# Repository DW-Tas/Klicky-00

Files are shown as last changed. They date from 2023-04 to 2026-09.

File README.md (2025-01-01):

[][cc-by-nc-sa]

# Klicky-00: Zero X,Y offset probe (RC3)

Building on the amazing work of JosAr ([Klicky Probe](https://github.com/jlas1/Klicky-Probe)), whoppingpochard ([PCB Klicky](https://github.com/tanaes/whopping_Voron_mods/tree/main/pcb_klicky)), and Majarspeed ([Unklicky](https://github.com/majarspeed/Unklicky)) this mod moves the probe directly under the nozzle (X,Y 0,0) and also has the nozzle touching the probe so that you can reliably use it as your z endstop with consistent z-offset. All the usual caveats about clean nozzles during probing apply here too.

The goal of this probe is to give accurate, nozzle probe-like, repeatable Z-offset on a budget even when changing nozzles.

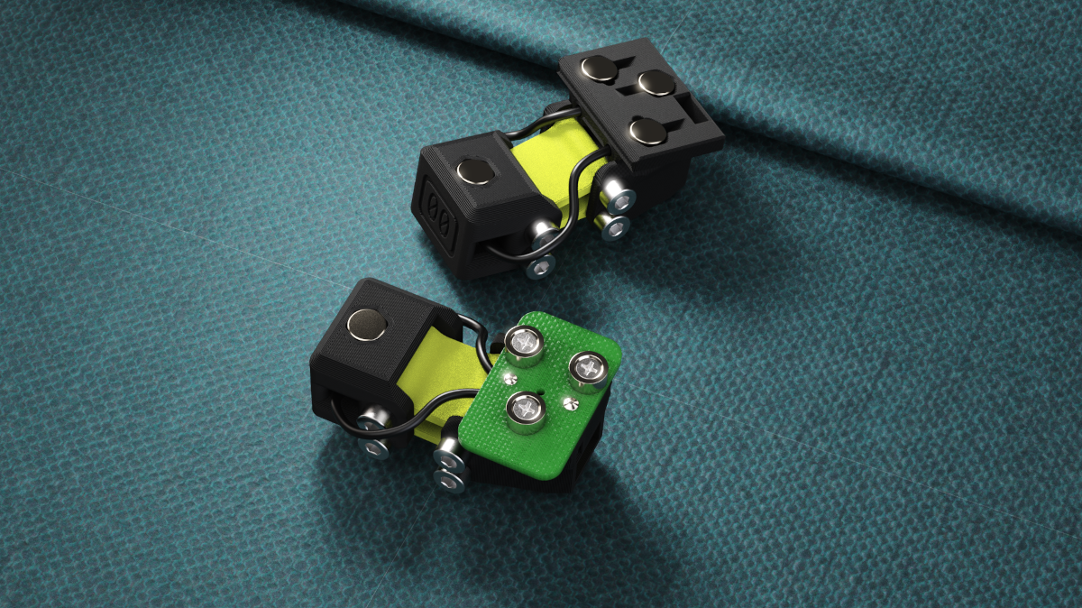
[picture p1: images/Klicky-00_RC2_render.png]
render

<br/> <br/>

<br/> <br/> <br/> <br/>
> [!NOTE]  
> You can help support the development of Klicky-00.<br/>
> Click on the Ko-Fi image below.<br/>

ko-fi (https://ko-fi.com/O5O5OCC0K)

<br/> <br/> <br/>

#### Constraints:
* Low cost
* Easy access to required parts
* Simple add-on to existing ecosystems

### Currently in "release candidate (RC)" status
Versions have been community tested on Xol Toolhead, Archetype and Stealthburner. Many gremlins have been worked out already, but things are still being found as more and more people join the fun of Klicky-00.

### Discussion and development on the Armchair discord

Join us on Discord (https://discord.gg/armchairengineeringsux)<br/>
Find the [Klicky-00 thread](https://discord.com/channels/1029426383614648421/1101496347540082799) under "user-projects"

#### RC3 - 01/01/2025
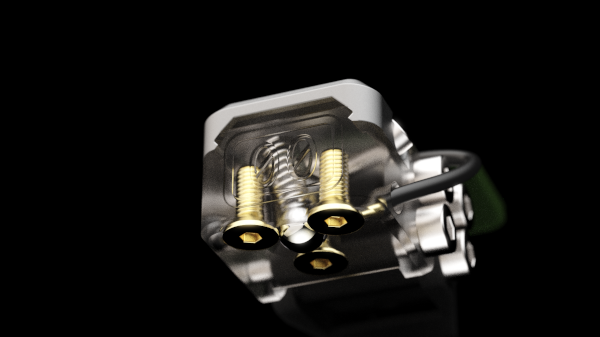
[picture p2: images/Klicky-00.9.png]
Buckshot transparent

* Swingarm fixes for better location of probe under nozzle
* Changed Buckshot switches to use FHCS screws
* CAD fixes

#### RC2 - 05/05/2024
* Changed swingarm hinge screws to M3 (no more M2.5 screws needed)
* Increased strength around hinge points
* Moved D2F switch location to properly match 0,0 concept
* `New Switch Type` `Beta` Buckshot switch by ZaMarin <br/><br/>
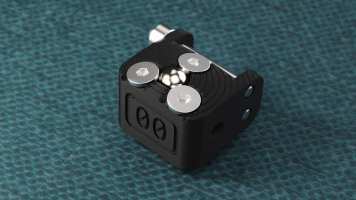
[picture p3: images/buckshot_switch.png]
buckshot switch
  

### Use 6mm x 3mm magnets
I have designed this around 6x3mm magnets and it will probably fail with the 6x2.7mm magnets that are also common. A mix of N52 and N35 magnets are most likely needed to help "tune" attraction and spring forces.

### Build Guide
Go to the [instructions](instructions.md)

### But why another probe?
Like many others, I installed Voron TAP and loved the consistency, repeatability and user experience, but I didn't like the extra complexity, weight and instability added to the toolhead.
I had previously used KlickyNG with auto-z calibration scripts and while that was good, I ALWAYS had to watch the first layer and make micro-adjustments to Z offset.

This probe takes the reliable docking hardware and software of the PCB Klicky and the high accuracy of the Unklicky BFP and puts them in contact with the probe for repatable z-offset and zero XY offset.

Initial testing in a Voron 2.4R2(300mm) with Xol-Toolhead looks promising.
probe_accuracy standard deviation results vary from 0.0005 to 0.0025 on my printer and that is similar to what I got with TAP.

Drift was also very low with bed temp at 118°C, nozzle 200°C and chamber ~57°C

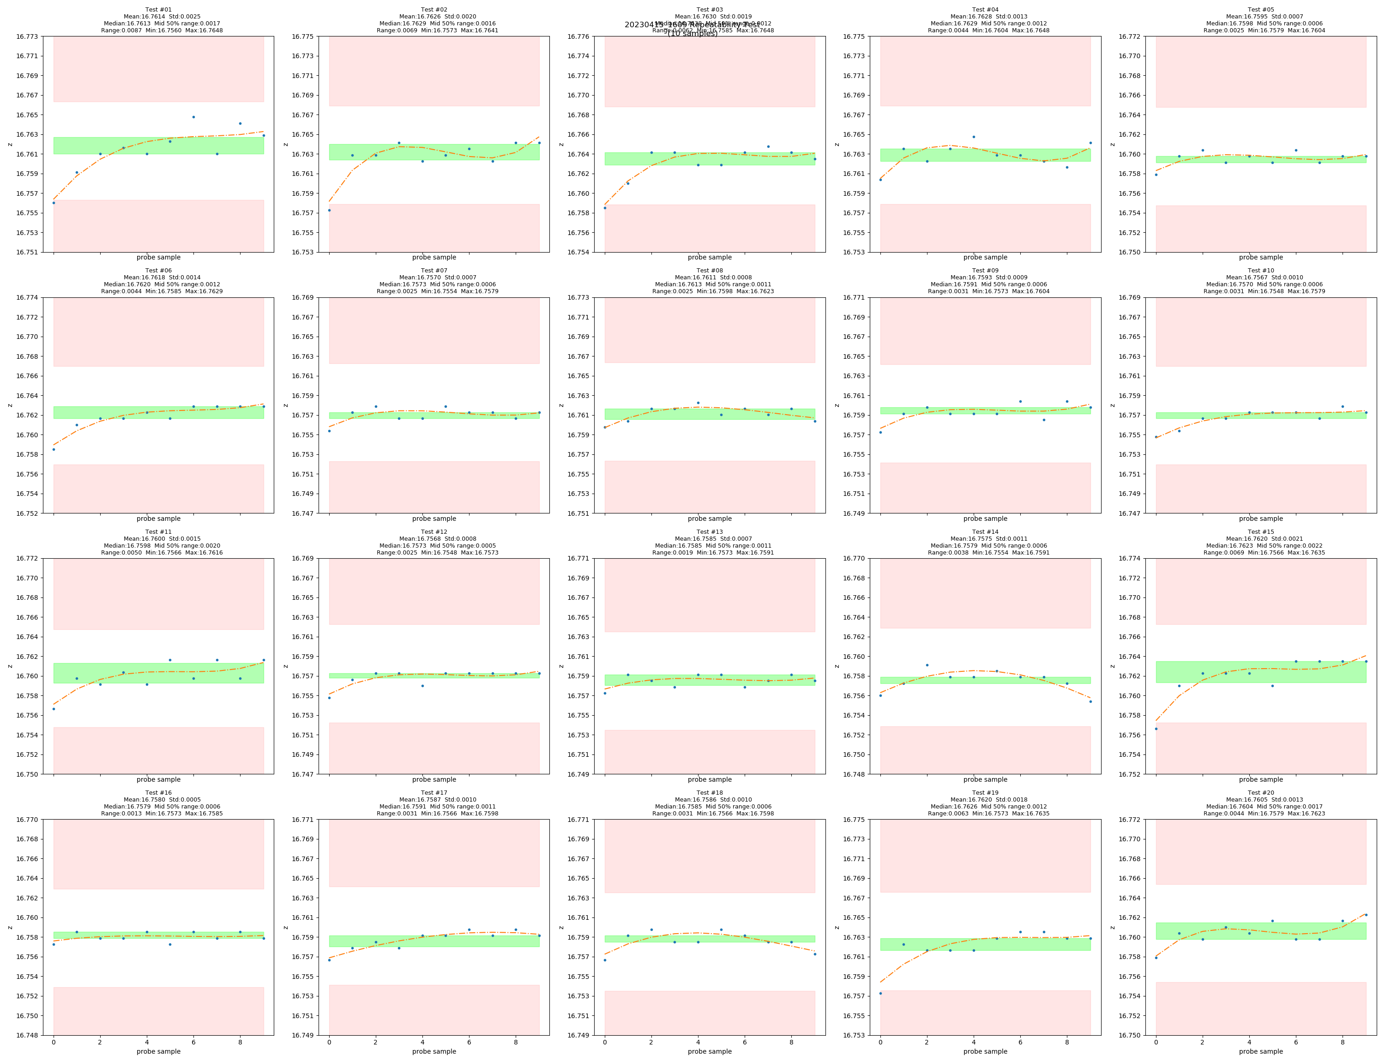
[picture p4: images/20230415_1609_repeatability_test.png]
repeatability_test

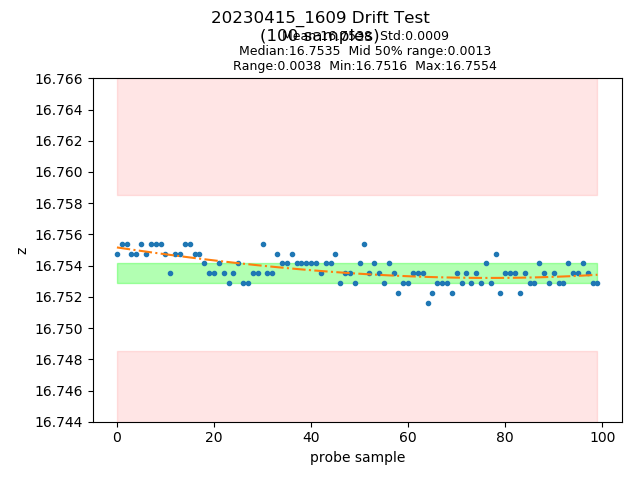
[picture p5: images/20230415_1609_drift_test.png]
drift_test


### Credits:
* ZaMarin - For the Buckshot switch mechanism, and inspiring the linkage design that unlocked Klicky-00s potential and the continued help behind the scenes.

### References:
* [Klicky Klipper macros](https://github.com/jlas1/Klicky-Probe/tree/main/Klipper_macros)
* [Unklicky build guide](https://github.com/majarspeed/Unklicky/blob/main/Build%20Guide.md)
* [Voron Docs Klicky as Z-endstop](https://docs.vorondesign.com/community/howto/Takuya/Klicky_Probe_AutoZ_Alternative.html)

<br/><br/><br/><br/>
This work is licensed under a
[Creative Commons Attribution-NonCommercial-ShareAlike 4.0 International License][cc-by-nc-sa].

[][cc-by-nc-sa]

[cc-by-nc-sa]: http://creativecommons.org/licenses/by-nc-sa/4.0/
[cc-by-nc-sa-image]: https://licensebuttons.net/l/by-nc-sa/4.0/88x31.png
[cc-by-nc-sa-shield]: https://img.shields.io/badge/License-CC%20BY--NC--SA%204.0-lightgrey.svg

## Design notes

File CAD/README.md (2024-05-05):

### Finally some release candidate CAD 😄

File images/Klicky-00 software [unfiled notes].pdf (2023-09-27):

# Klicky-00 software

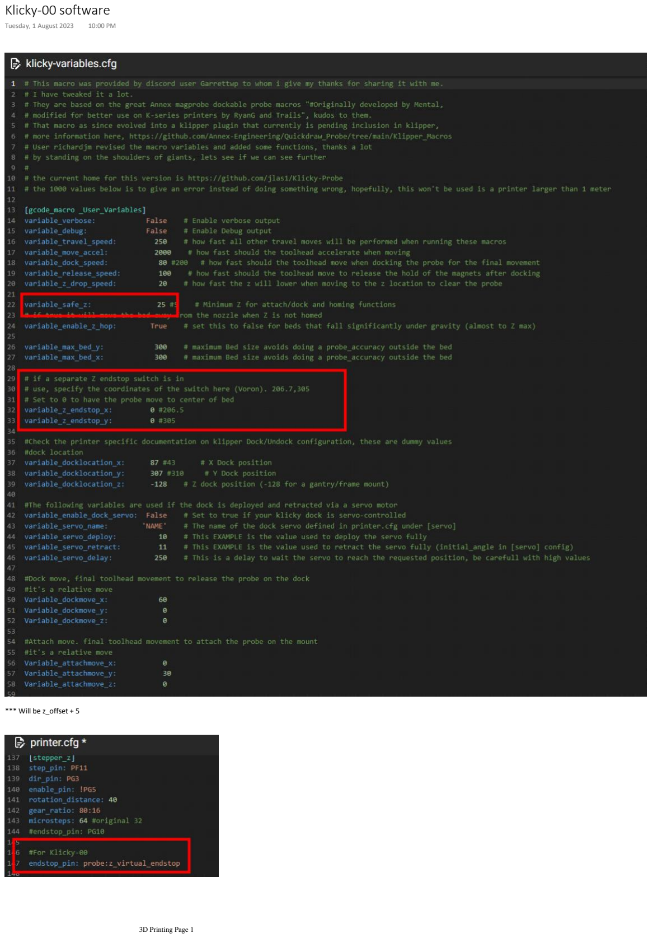
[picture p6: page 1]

*** Will be z_offset + 5

Tuesday, 1 August 2023 10:00 PM

3D Printing Page 1

****for setup only set "position_min: -25" (in the stepper_z section)
** DANGER: set this back to -5 after setup. You need to be able to go much further below zero when first doing "probe_calibrate" with Klicky-00

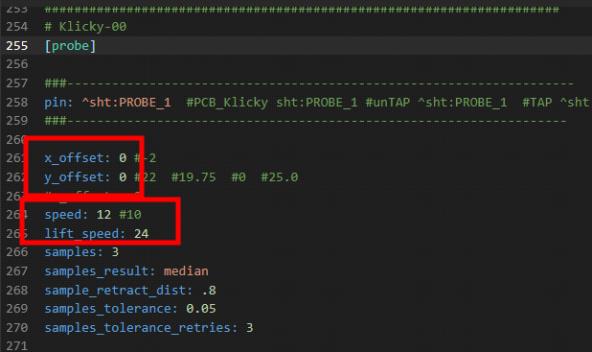
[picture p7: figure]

* [z_offset] +5 is pretty safe

*[z_offset] + retract distance gives fasted mesh

****** After running probe_calibrate locate z_offset that was saved at the end of printer.cfg

3D Printing Page 2

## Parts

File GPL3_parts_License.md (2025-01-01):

The custom STLs that come from GPL3 projects remain under the GPLv3 license.
<br/><br/>
These parts are the rear parts of the probe that include the Klicky and Klicky PCB docking and attachment geometry:
* Klicky-00_Klicky_Rear
* Klicky-00_PCB_Klicky_Rear

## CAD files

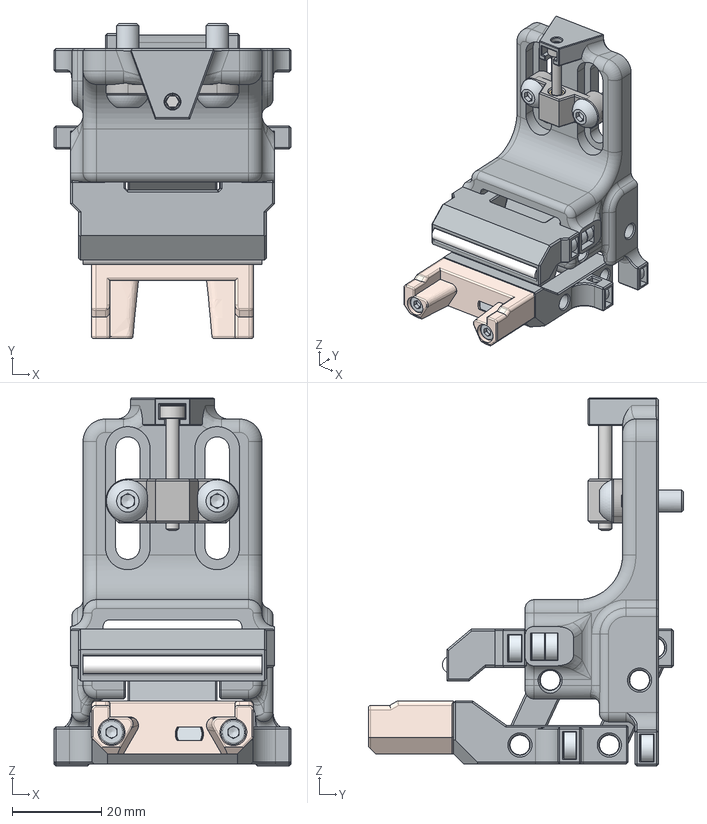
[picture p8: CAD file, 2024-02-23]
CAD/Klicky-00_Bump-Dock_assembly.step
53.0 x 70.4 x 82.3 mm
Klicky-00_front_magnet x 5
Lowerbody
PTFE Tube
arm1
Socket button head screw M5x0.8 x 16 x 2
M3 Threaded Insert (1) v1 x 3
height-adjuster
M3x25 SHCS
Mainbody
bumper
Klicky-00 PCB dock
Klicky-00_rear_magnet
Hex socket head cap screw M3x0.50 x 20 x 2
arm2

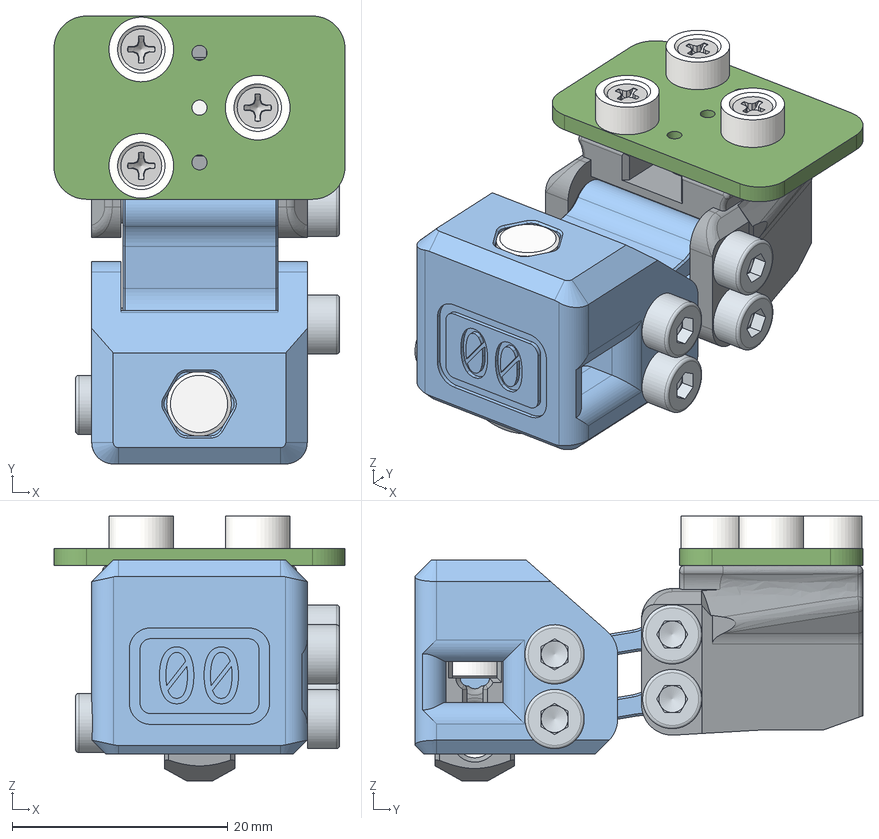
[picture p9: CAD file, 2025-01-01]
CAD/Klicky-00 - RC3 Assembled probes/Klicky-00 Archetype Unklicky PCB.step
27.0 x 41.6 x 24.6 mm
Klicky-00_Archetype_Swingarm_Lower
Klicky-00_Archetype_Swingarm_Upper
Hex socket head cap screw M3x0.50 x 20 x 4
Klicky-00_Archetype_Unklicky_Front
Klicky-00_Unklicky_Stylus
Hex socket head cap screw M3x0.50 x 12
6x3 Magnet x 5
Klicky-00_PCB_Klicky_Rear
pcb
94180A307_Tapered Heat-Set Inserts for Plastic x 3
Magnets x 3
91420A003_Steel Phillips Flat Head Screws x 3

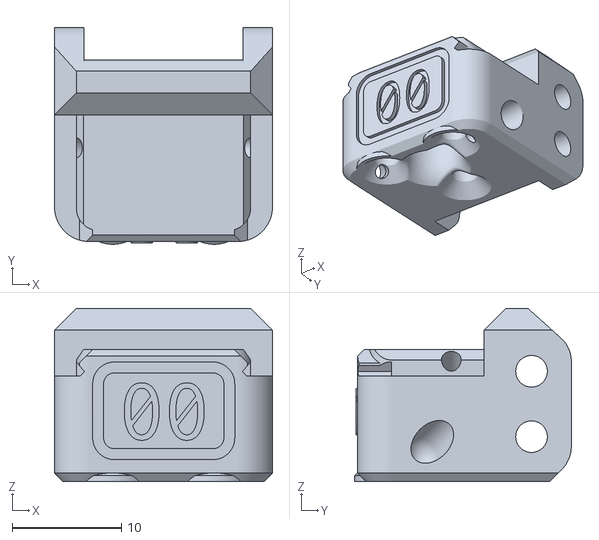
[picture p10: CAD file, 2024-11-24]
STL/SLM Nozzle Plate/Klicky-00_A4T-Xol_Buckshot_Front-Strike_SLM.stl
20.0 x 19.9 x 15.9

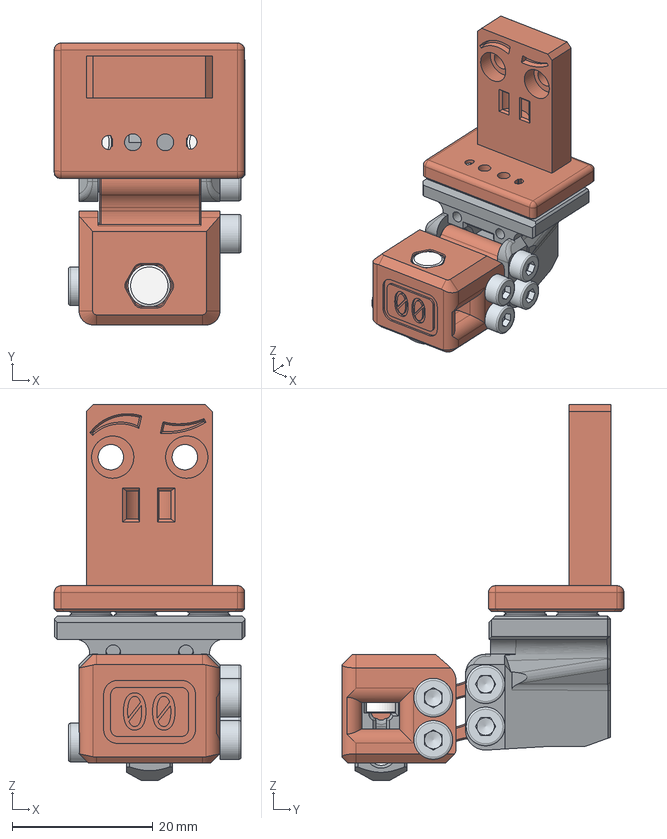
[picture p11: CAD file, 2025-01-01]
CAD/Klicky-00 - RC3 Assembled probes/Klicky-00 SB Unklicky Klicky.step
27.1 x 40.0 x 53.3 mm
Klicky-00_SB_Swingarm_Upper
6x3 Magnet x 11
Klicky-00_SB_Swingarm_Lower
Hex socket head cap screw M3x0.50 x 20 x 4
Klicky-00_Klicky_Rear
Klicky-00_Klicky_Mount_SB
Klicky-00_Unklicky_Stylus
Klicky-00_SB_Unklicky_Front
Hex socket head cap screw M3x0.50 x 12

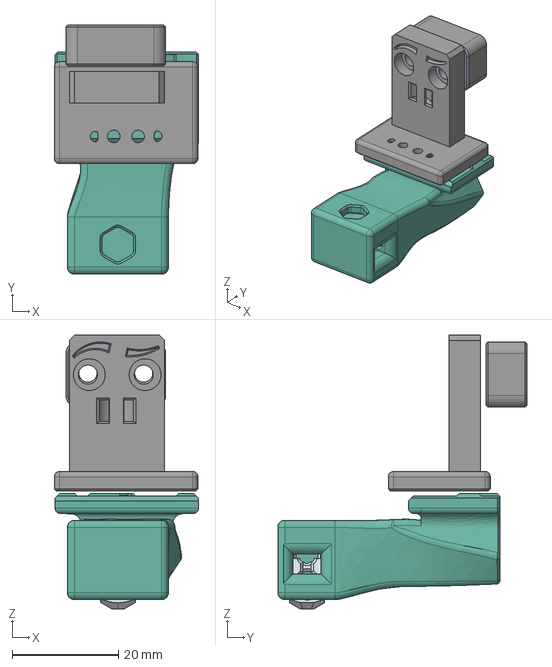
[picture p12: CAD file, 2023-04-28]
CAD/Klicky-00_SB.step
27.2 x 47.0 x 51.6 mm

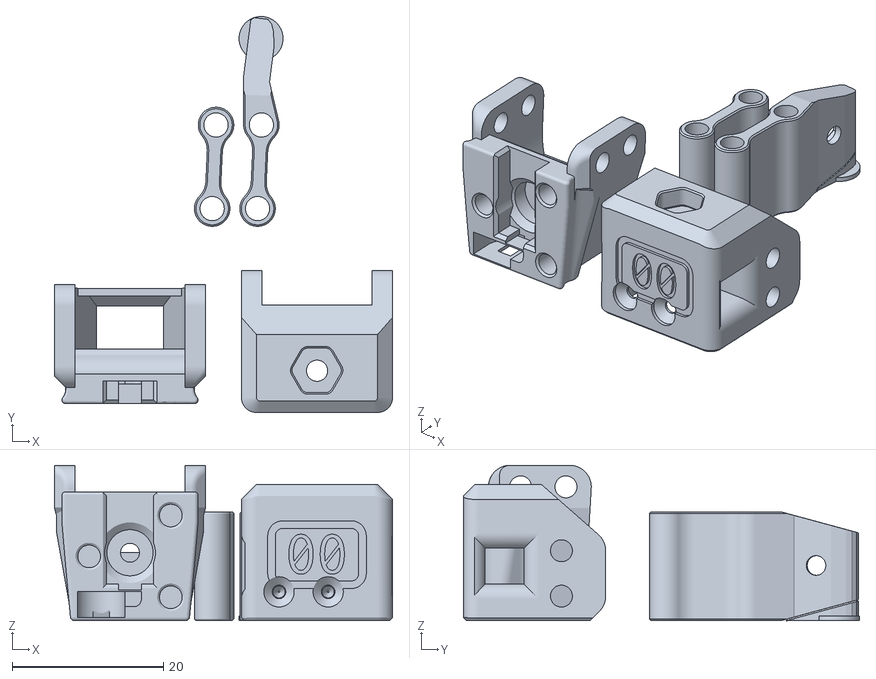
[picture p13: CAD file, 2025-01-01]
STL/Archetype - D2F - PCB.stl
44.7 x 52.4 x 20.5

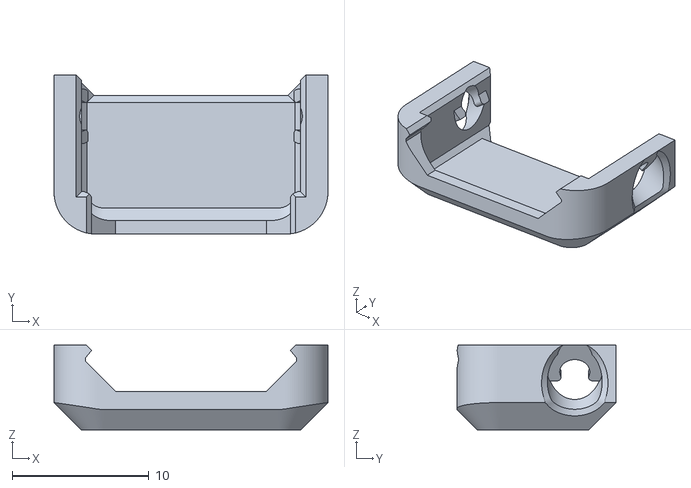
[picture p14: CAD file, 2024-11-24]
STL/SLM Nozzle Plate/Klicky-00_SLM_Nozzle_Plate.stl
20.0 x 11.6 x 6.20

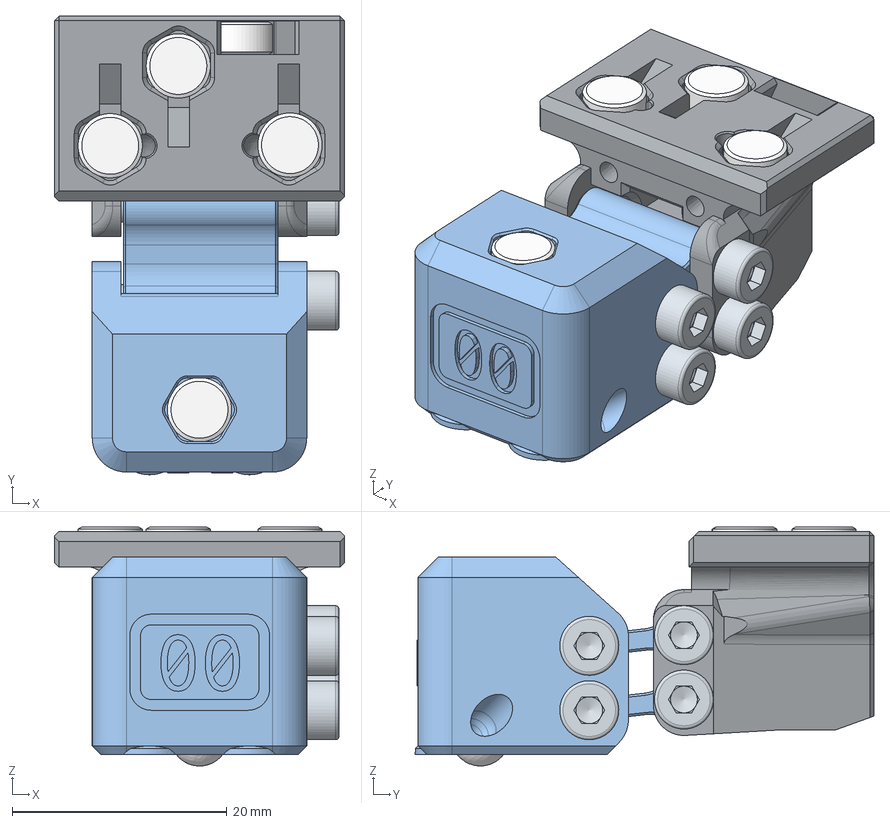
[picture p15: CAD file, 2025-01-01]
CAD/Klicky-00 - RC3 Assembled probes/Klicky-00 Archetype Buckshot Klicky.step
27.0 x 42.7 x 22.3 mm
6x3 Magnet x 7
Klicky-00_Archetype_Swingarm_Lower_Buckshot
Klicky-00_Archetype_Swingarm_Upper_Buckshot
Hex socket head cap screw M3x0.50 x 20 x 4
Klicky-00_Archetype_Buckshot_Front
BB
M3x8 FHCS x 3
Spring
Klicky-00_Klicky_Rear

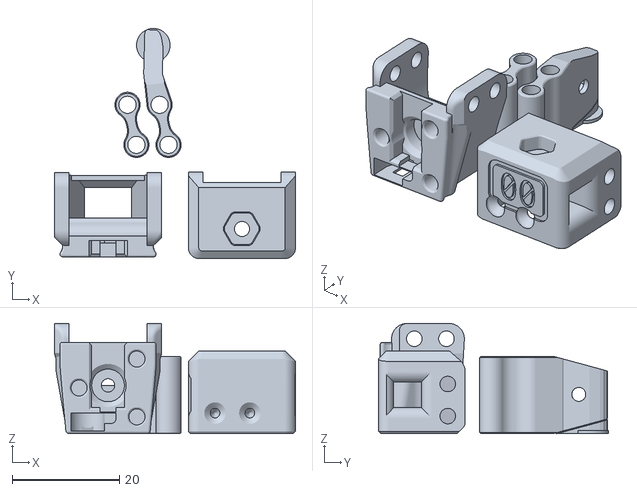
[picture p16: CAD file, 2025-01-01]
STL/StealthBurner - D2F - PCB.stl
45.0 x 43.0 x 20.5

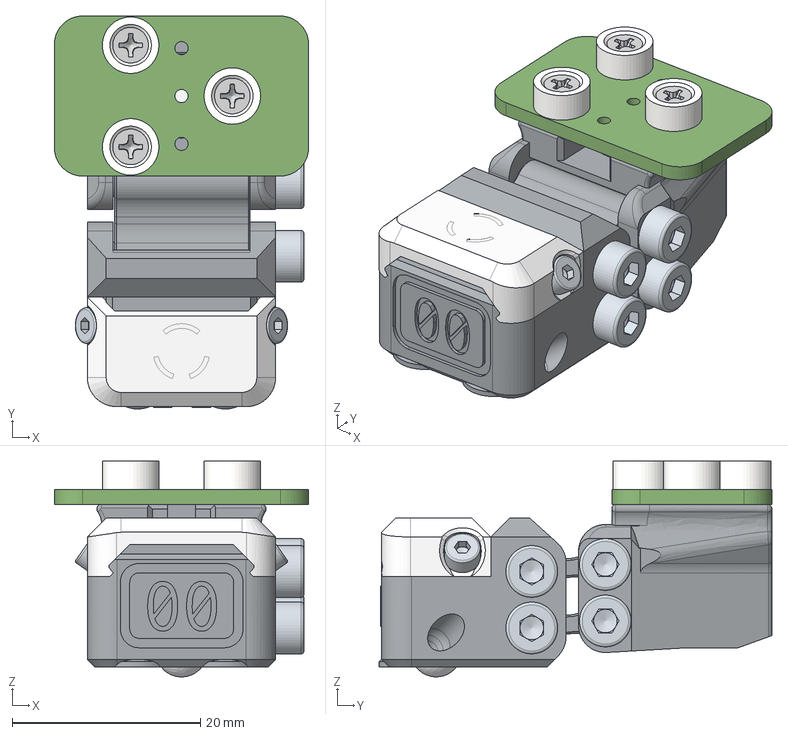
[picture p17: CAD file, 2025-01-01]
CAD/Klicky-00 - RC3 Assembled probes/Klicky-00 Xol Buckshot SLM PCB.step
27.0 x 41.7 x 22.9 mm
Klicky-00_Xol_PCB_Swingarm_Upper_Buckshot
6x3 Magnet x 3
Klicky-00_Xol_PCB_Swingarm_Lower_Buckshot
Hex socket head cap screw M3x0.50 x 20 x 4
Hex socket head cap screw M2x0.40 x 6 x 2
SLM Strike Plate
Klicky-00_Xol_Buckshot_Front_SLM_Strike
BB
Spring
M3x8 FHCS x 3
pcb
94180A307_Tapered Heat-Set Inserts for Plastic x 3
Magnets x 3
91420A003_Steel Phillips Flat Head Screws x 3
Klicky-00_PCB_Klicky_Rear

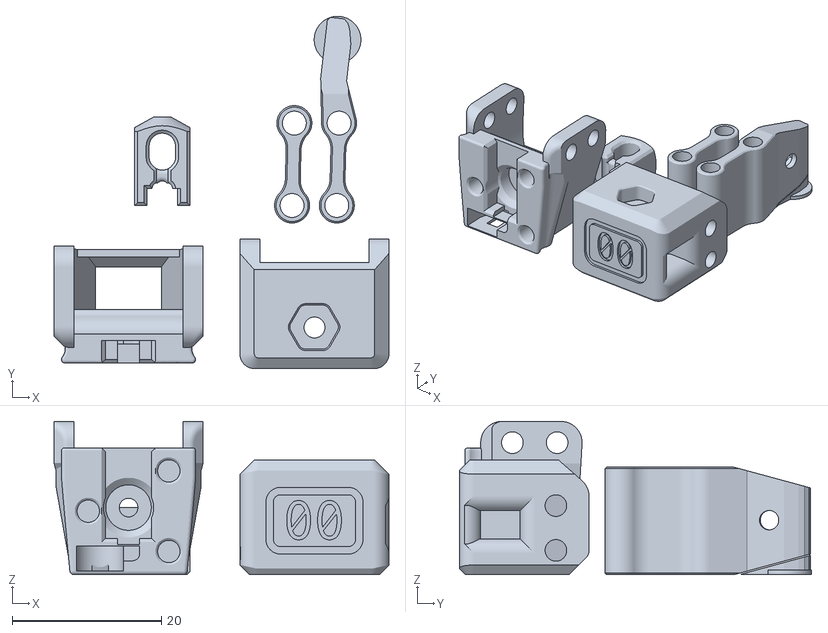
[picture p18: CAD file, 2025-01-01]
STL/A4T-Xol - Unklicky - PCB.stl
44.9 x 47.2 x 20.5

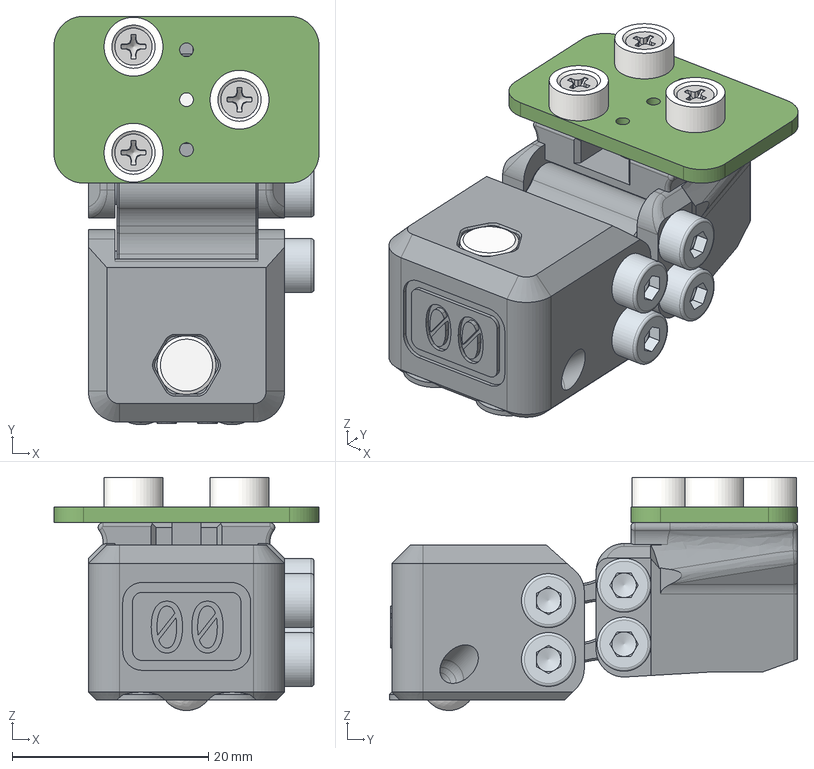
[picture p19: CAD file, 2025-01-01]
CAD/Klicky-00 - RC3 Assembled probes/Klicky-00 Xol Buckshot PCB.step
27.0 x 41.6 x 23.7 mm
Klicky-00_Xol_PCB_Swingarm_Upper_Buckshot
6x3 Magnet x 4
Klicky-00_Xol_PCB_Swingarm_Lower_Buckshot
Hex socket head cap screw M3x0.50 x 20 x 4
Klicky-00_Xol_Buckshot_Front
BB
Spring
M3x8 FHCS x 3
pcb
94180A307_Tapered Heat-Set Inserts for Plastic x 3
Magnets x 3
91420A003_Steel Phillips Flat Head Screws x 3
Klicky-00_PCB_Klicky_Rear

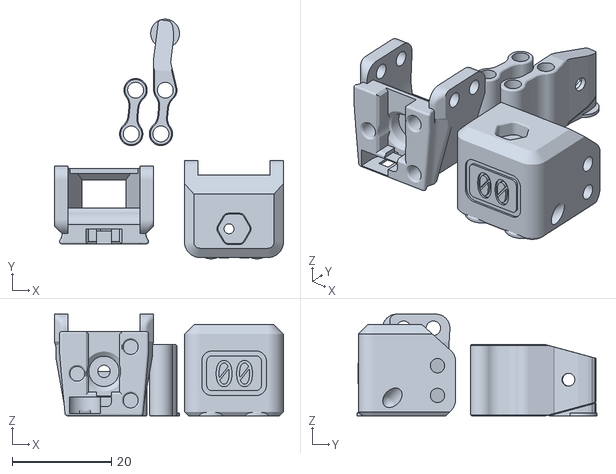
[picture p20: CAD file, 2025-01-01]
STL/Archetype - Buckshot - PCB.stl
46.2 x 48.4 x 20.5

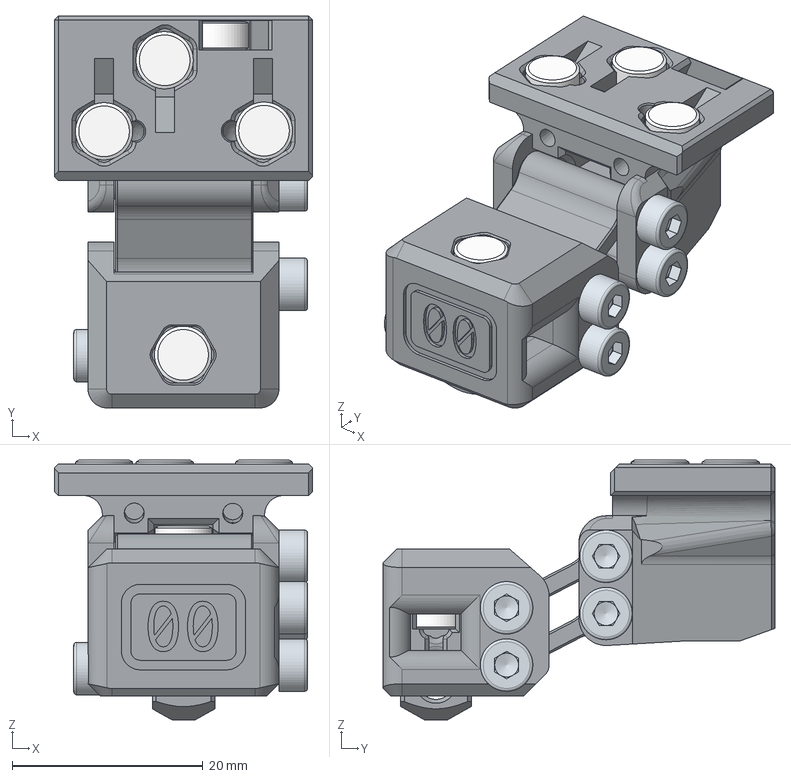
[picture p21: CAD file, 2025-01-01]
CAD/Klicky-00 - RC3 Assembled probes/Klicky-00 Xol Unklicky Klicky.step
27.0 x 41.1 x 27.2 mm
Klicky-00_Xol_Swingarm_Upper
Hex socket head cap screw M3x0.50 x 20 x 4
Hex socket head cap screw M3x0.50 x 12
6x3 Magnet x 8
Klicky-00_Xol_Unklicky_Front
Klicky-00_Unklicky_Stylus
Klicky-00_Xol_Swingarm_Lower
Klicky-00_Klicky_Rear

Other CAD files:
CAD/Klicky-00 - RC3 Assembled probes/Klicky-00 Xol Unklicky PCB.step
STL/StealthBurner - D2F - Klicky.stl
CAD/Klicky-00 - RC3 Assembled probes/Klicky-00 SB Buckshot Klicky.step
CAD/Klicky-00 - RC3 Assembled probes/Klicky-00 Archetype Buckshot PCB.step
CAD/Klicky-00 - RC3 Assembled probes/Klicky-00 Archetype D2F Klicky.step
CAD/Klicky-00 - RC3 Assembled probes/Klicky-00 Archetype D2F PCB.step
CAD/Klicky-00 - RC3 Assembled probes/Klicky-00 Archetype Unklicky Klicky.step
CAD/Klicky-00 - RC3 Assembled probes/Klicky-00 SB Buckshot PCB.step
CAD/Klicky-00 - RC3 Assembled probes/Klicky-00 SB D2F Klicky.step
CAD/Klicky-00 - RC3 Assembled probes/Klicky-00 SB D2F PCB.step
CAD/Klicky-00 - RC3 Assembled probes/Klicky-00 SB Unklicky PCB.step
CAD/Klicky-00 - RC3 Assembled probes/Klicky-00 Xol Buckshot Klicky.step
CAD/Klicky-00 - RC3 Assembled probes/Klicky-00 Xol Buckshot SLM Klicky.step
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

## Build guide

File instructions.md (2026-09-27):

# Build Instructions

> [!WARNING]
> You need to have a good understanding of Klicky (+macro settings), probes, offsets and Klipper.

It is highly recommended to have a working PCB Klicky or standard Klicky already installed on your toolhead and configured. Follow the instructions from Josar on the Klicky-Probe Github:
[klipper configuration](https://github.com/jlas1/Klicky-Probe/tree/main/Printers/Voron/v1.8_v2.4_Legacy_Trident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) \
Make sure to include the steps for [Klicky Probe as Endstop with constant Z-Offset](https://github.com/T4KUUY4/Voron-Stuff/tree/main/KlickyProbeZoffset).

> [!IMPORTANT]
> Klicky-00 is a Loooong probe. It doesn't fit behind the print bed of a standard Voron 2.4 or Trident build without a dock that retracts the probe. See "Bump dock" instructions below.
> `Should be OK with StealthBurner version as the probe is ~5.5mm shorter`

> [!WARNING]
> You need at least 5mm travel on Y past the back of your build plate for this to work.

## Klicky-00 Probe

The probe is built from components of other projects. The original concept of this project is putting the probe under the nozzle in a repeatable/automatable way.

## BOM

The first two tables are specific to the mount type you use. The third table has extra BOM depending on switch type.

### PCB Klicky Version (needed for all switch types)

`[Assumes you already have the PCB Klicky upper mount on your toolhead]`

| Qty | Item | Note |
| --- | --- | --- |
| 1 | PCB Klicky Lower kit | Lower PCB with switch removed, magnets, screws and heatset inserts that came with the kit or equivalent |
| 5 | 6x3mm Disc Magnets | Probably a mix of N52 and N35 strength for adjustability |
| 4 | M3 x 20mm SHCS or BHCS | Swing arm hinges |
| 2 | Lengths of wire | Less than 2mm sheathing diameter, approx 100mm |

### Standard Klicky Version (needed for all switch types)

`[Assumes you already have the Klicky mount on your toolhead]`

| Qty | Item | Note |
| --- | --- | --- |
| 8 | 6x3mm Disc Magnets | Probably a mix of N52 and N35 strength for adjustability |
| 4 | M3 x 20mm SHCS or BHCS | Swing arm hinges |
| 2 | Lengths of wire | Less than 2mm sheathing diameter, approx 100mm |

### Extra parts by switch type

| Switch Type | Qty | Item | Note |
| :--- | --- | --- | --- |
| Buckshot | 3 | M3 x 8 FHCS `M3 x 6 FHCS will work` | Brass version from Ali Express (https://www.aliexpress.com/item/1005004957093547.html) |
| Buckshot | 1 | 5.5m Ball Bearing | Known good source from Ali Express (https://www.aliexpress.com/item/1005005046697375.html) |
| Buckshot | 1 | Spring: <br/>* Length: 10mm<br/>* Wire Diameter: 0.4mm<br/>* Outer Diameter: 4mm | Known good source from Ali Express (https://www.aliexpress.com/item/1005007100755870.html) |
| Unklicky | 1 | M3 x 12mm SHCS | Unklicky probe stylus retention screw |
| D2F | 1 | D2F switch | No lever |
| D2F | 2 | M2 x 10mm self tapping countersunk screws | |

## Printed Parts
Pick your toolhead, switch type and mount type from the tables below to find the correct file to print

#### A4T or Xol-Toolhead
| | Klicky PCB | Klicky Standard |
| --- | --- | --- |
| Buckshot | [A4T-Xol - Buckshot - PCB.stl](<STL/A4T-Xol - Buckshot - PCB.stl>) | [A4T-Xol - Buckshot - Klicky.stl](<STL/A4T-Xol - Buckshot - Klicky.stl>) |
| Unklicky | [A4T-Xol - Unklicky - PCB.stl](<STL/A4T-Xol - Unklicky - PCB.stl>) | [A4T-Xol - Unklicky - Klicky.stl](<STL/A4T-Xol - Unklicky - Klicky.stl>) |
| D2F | [A4T-Xol - D2F - PCB.stl](<STL/A4T-Xol - D2F - PCB.stl>) | [A4T-Xol - D2F - Klicky.stl](<STL/A4T-Xol - D2F - Klicky.stl>) |
#### Archetype
| | Klicky PCB | Klicky Standard |
| --- | --- | --- |
| Buckshot | [Archetype - Buckshot - PCB.stl](<STL/Archetype - Buckshot - PCB.stl>) | [Archetype - Buckshot - Klicky.stl](<STL/Archetype - Buckshot - Klicky.stl>) |
| Unklicky | [Archetype - Unklicky - PCB.stl](<STL/Archetype - Unklicky - PCB.stl>) | [Archetype - Unklicky - Klicky.stl](<STL/Archetype - Unklicky - Klicky.stl>) |
| D2F | [Archetype - D2F - PCB.stl](<STL/Archetype - D2F - PCB.stl>) | [Archetype - D2F - Klicky.stl](<STL/Archetype - D2F - Klicky.stl>) |
#### StealthBurner
| | Klicky PCB | Klicky Standard |
| --- | --- | --- |
| Buckshot | [StealthBurner - Buckshot - PCB.stl](<STL/StealthBurner - Buckshot - PCB.stl>) | [StealthBurner - Buckshot - Klicky.stl](<STL/StealthBurner - Buckshot - Klicky.stl>) |
| Unklicky | [StealthBurner - Unklicky - PCB.stl](<STL/StealthBurner - Unklicky - PCB.stl>) | [StealthBurner - Unklicky - Klicky.stl](<STL/StealthBurner - Unklicky - Klicky.stl>) |
| D2F | [StealthBurner - D2F - PCB.stl](<STL/StealthBurner - D2F - PCB.stl>) | [StealthBurner - D2F - Klicky.stl](<STL/StealthBurner - D2F - Klicky.stl>) |
#### Extras
| File | Description |
| --- | --- |
| [StealthBurner - Klicky_Toolhead_Mount.stl](<STL/StealthBurner - Klicky_Toolhead_Mount.stl>) | Klicky mount to use with standard StealthBurner carriage when using the "standard Klicky" mount type with Klicky-00 |
| [Klicky-00_SLM_Nozzle_Plate.stl](<STL/SLM Nozzle Plate/Klicky-00_SLM_Nozzle_Plate.stl>) | SLM Strike plate version for A4T or Xol-Toolhead |
| [Klicky-00_A4T-Xol_Buckshot_Front-Strike_SLM.stl](<STL/SLM Nozzle Plate/Klicky-00_A4T-Xol_Buckshot_Front-Strike_SLM.stl>) | SLM Strike plate version for A4T or Xol-Toolhead |

## Instructions (PCB_Klicky Version with Unklcy switch)
| Note | Picture |
| --- | --- |
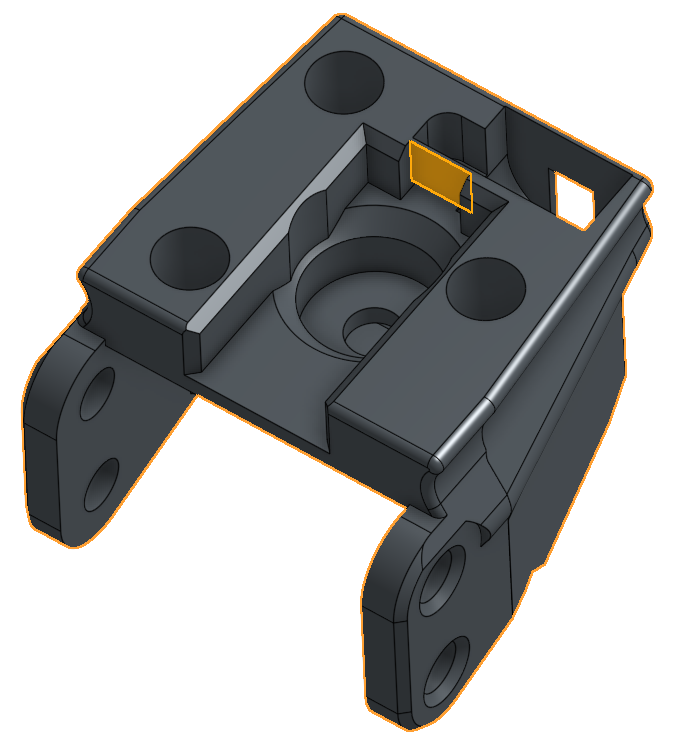
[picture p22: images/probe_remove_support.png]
| Remove the built in support |  |
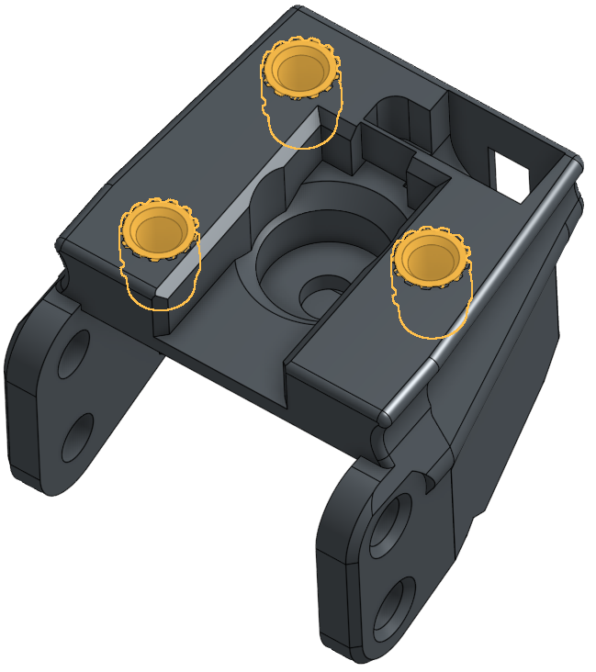
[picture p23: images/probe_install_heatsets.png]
| Install the M2 heatset inserts |  |
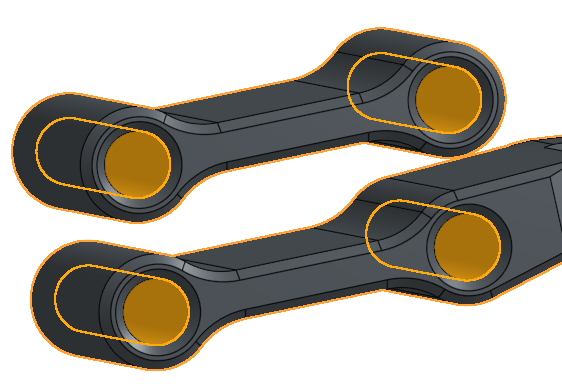
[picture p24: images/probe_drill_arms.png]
| If an M3 screw placed through the swing arms doesn't move freely with low friction, drill out the swing arm holes with M3 drill bit.<br/>`Don't over do it! If the screws have too much room the probe will end up wobbly and not be as accurate.` |  |
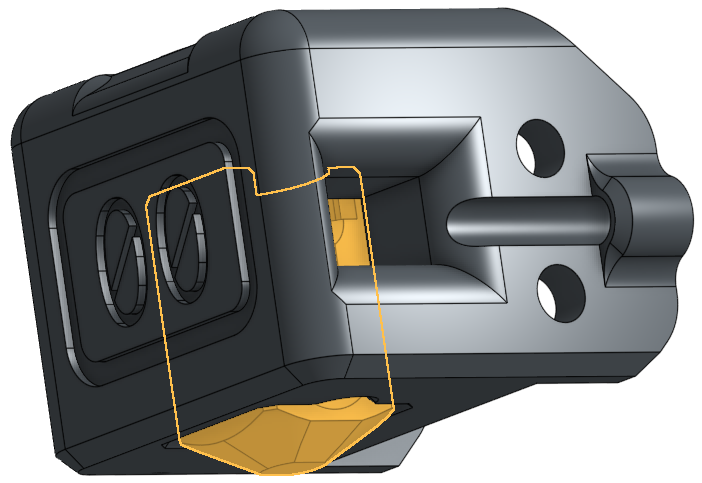
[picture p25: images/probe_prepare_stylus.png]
| Prepare the probe stylus. Sand it down so it moves smoothly inside the probe front body `Unklicky Version` |  |
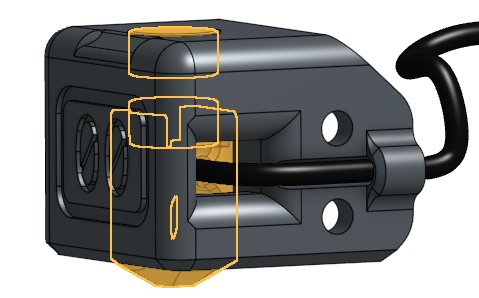
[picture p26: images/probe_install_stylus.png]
| Install the stylus as per UnKlickyBFP. Wire wraps around top of stylus, Magnets are opposing<br/>`*TIP: Make sure that the top magnet repells the furthest back magnet on the toolhead. This will make sure that Klicky-00 is pushed down as the toolhead moves over it to attach the probe.` |  |
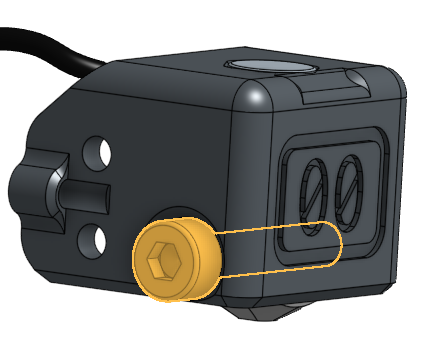
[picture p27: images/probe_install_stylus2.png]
| Put the screw in most of the way. Leave room for the second wire to wrap around |  |
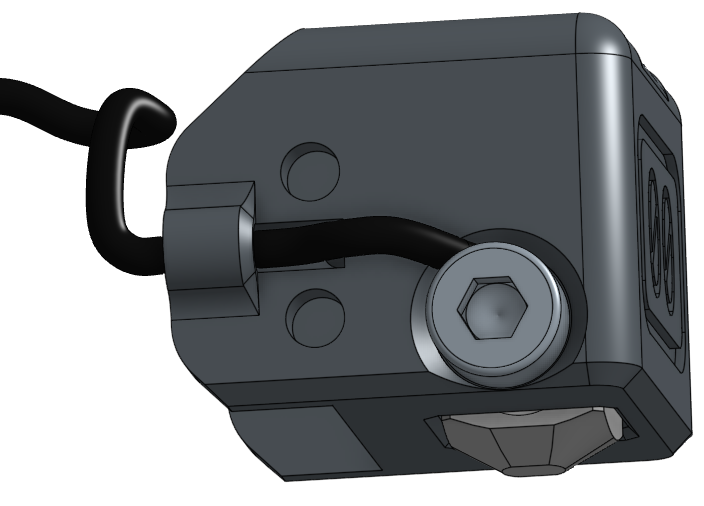
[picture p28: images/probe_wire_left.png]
| Put the left side wire in place, wrapped around the screw and tighten the screw |  |
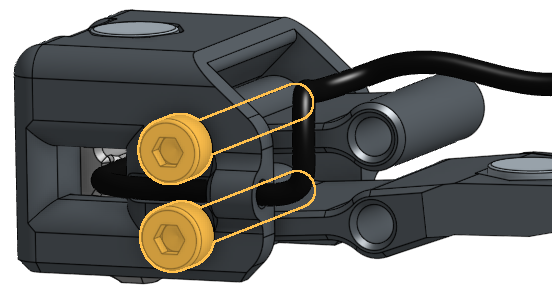
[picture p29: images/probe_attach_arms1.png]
| Install the front two swing arm screw hinges |  |
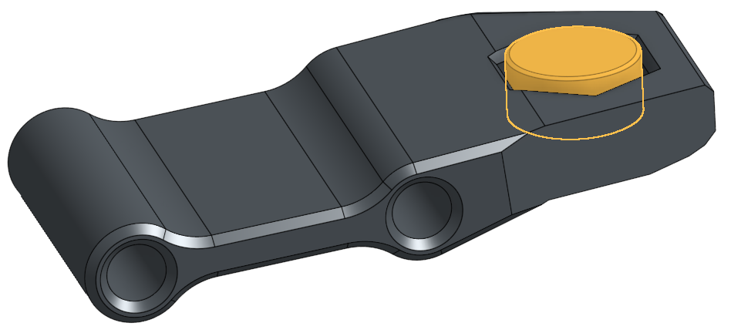
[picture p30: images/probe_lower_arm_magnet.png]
| Install a magnet in the back of the lower swing arm |  |
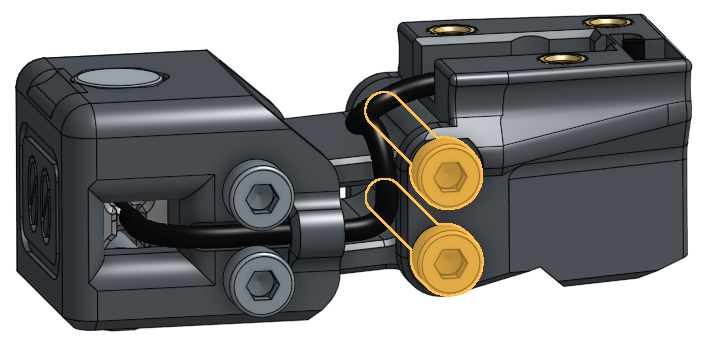
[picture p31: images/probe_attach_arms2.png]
| Install the other two swing arm screws |  |
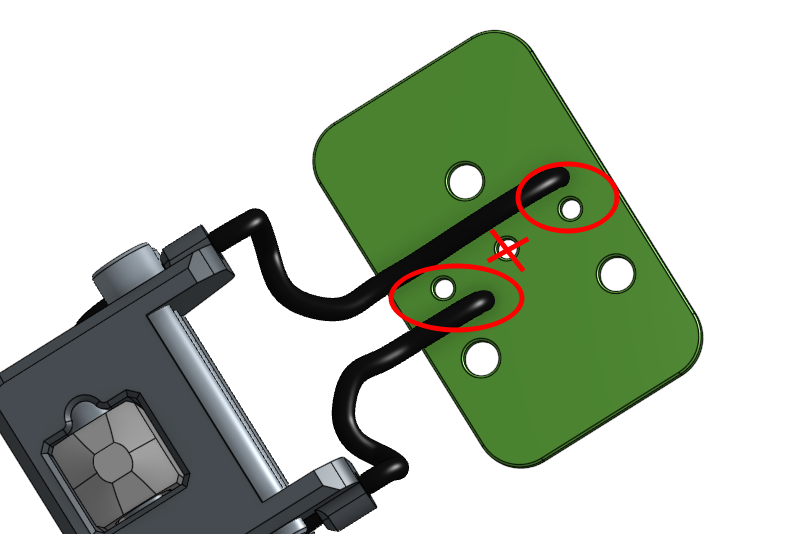
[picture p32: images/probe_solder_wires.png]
| Solder the probe wires to the bottom of the PCB Klicky lower PCB. One in the front, one at the back. Middle hole stays empty |  |
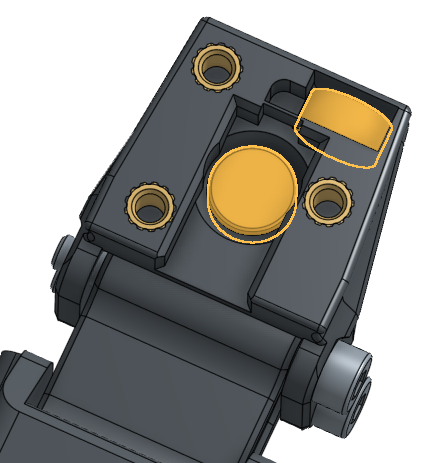
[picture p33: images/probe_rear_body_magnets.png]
| Install the magnets that live under the PCB. The rear one should attract to the dock, the other should repel the lower swing arm. You may need to swap between N35 and N52 magnets to get just enough spring force to activate the swing arm. Too much won't let the arm move and will push the klicky PCB magnets apart. |  |
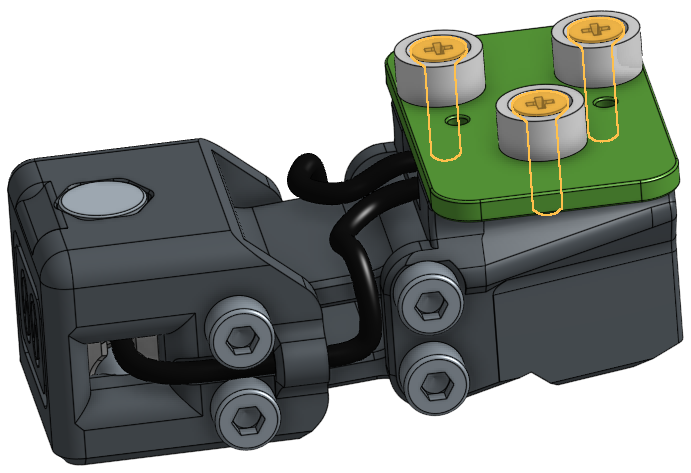
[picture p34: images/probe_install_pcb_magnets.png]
| Install the Klicky PCB magnets with the counter sunk screws. Get your polarity right. |  |

## Instructions (Standard Klicky Version)

[Todo (sorry)]

# Bump dock

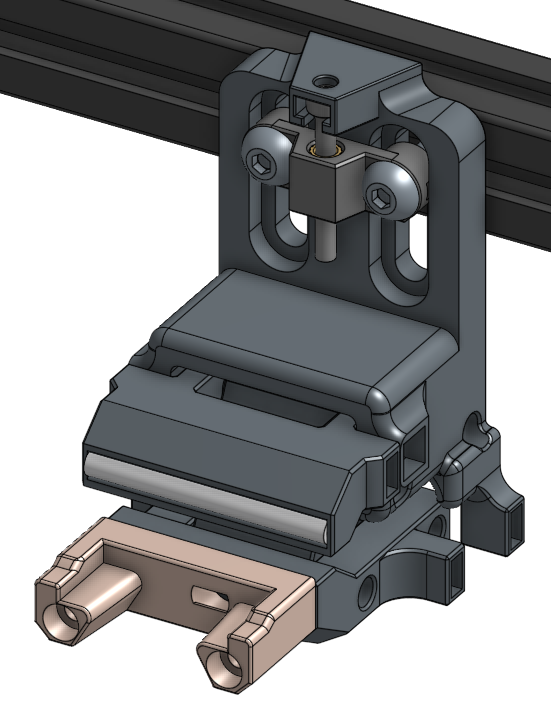
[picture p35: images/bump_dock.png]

In the spirit of Unklikcy, this atrocity is put together out of things that hopefully you have laying around as spare parts.

Like the rest of Klicky-00, magnets are used as "springs" because they're magic.

## BOM

| Qty | Item | Note |
| --- | --- | --- |
| 2 | M5 x 16 BHCS | Attaching to gantry |
| 2 | M5 T-Nuts | Attaching to gantry |
| 1 | M3 Heatset Insert | Standard Voron spec. In the height adjuster-a-thingy |
| 1 | M3 x 30 SHCS | Height adjustment screw |
| 2 | M3 Heatset Insert | Standard Voron spec. In the front of the klicky dock hoder |
| 2 | 36mm PTFE Tube | 2mm ID / 4mm OD PTFE Tube: lower hinges |
| 3 | 40mm PTFE Tube | 2mm ID / 4mm OD PTFE Tube: Middle hinges + Bump slide |
| 2 | 30mm PTFE Tube | 2mm ID / 4mm OD PTFE Tube: Upper hinges |
| 5 or 10 | 6x3mm Magnets | Depending on how strong the magnets are: the "Springs" for the bumber |
| 2 | M3x20 SHCS | Klicky dock to bump dock |
| 1 | 6x3mm Magnet | Behind Klicky dock |

## Instructions

| Note | Picture |
| --- | --- |
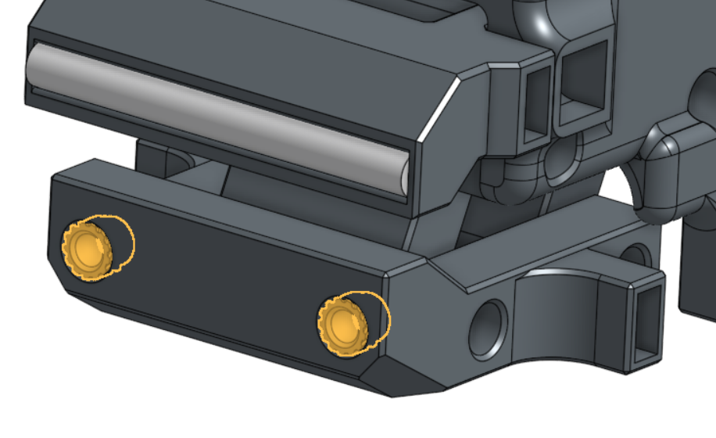
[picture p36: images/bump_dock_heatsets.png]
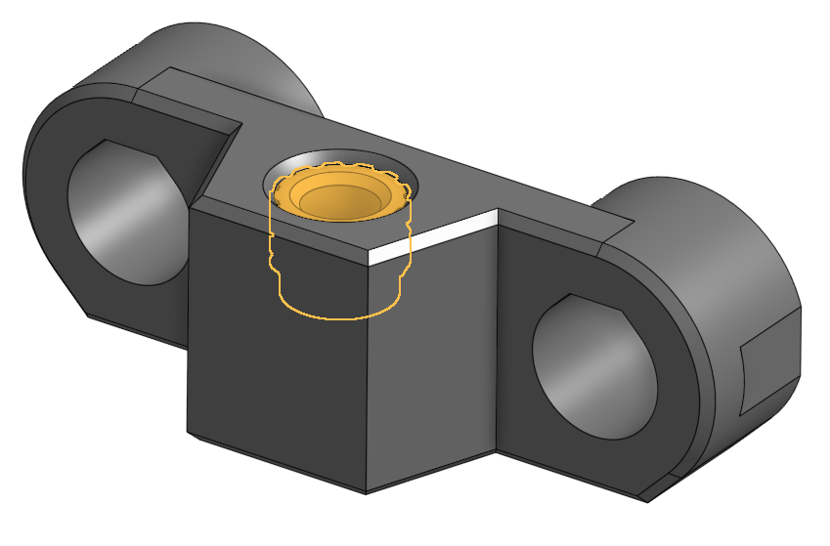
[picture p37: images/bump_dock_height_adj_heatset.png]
| Install heatset inserts:<br/> * Lower arm and height adjuster |  <br/>   |
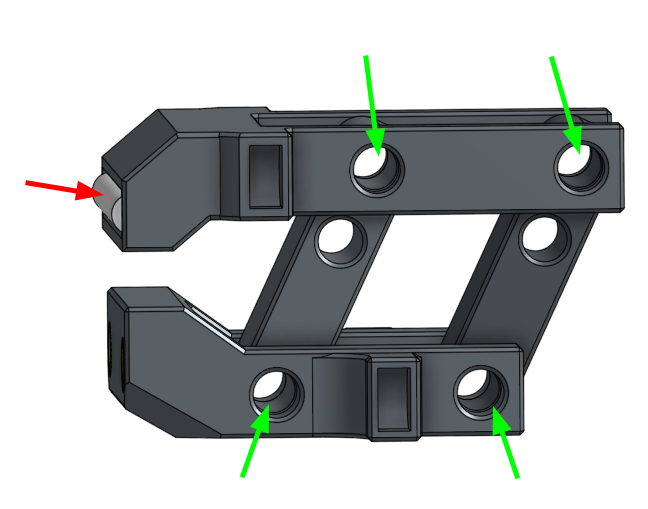
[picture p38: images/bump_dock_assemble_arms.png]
| Put the dock arms together with the PTFE tube in the upper and lower hinges. Don't forget the other PTFE tube on the front of the bumper! |  |
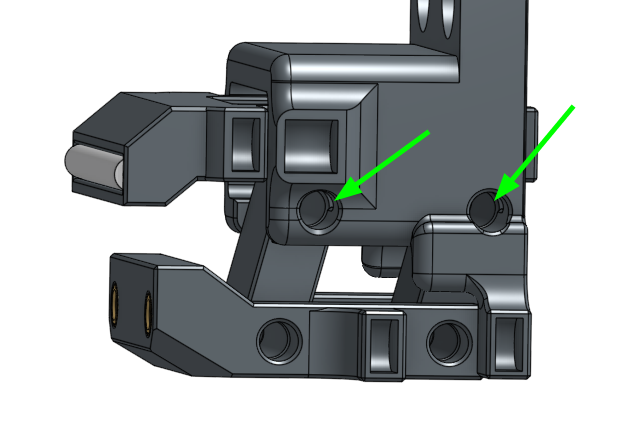
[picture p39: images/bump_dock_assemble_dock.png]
| Slide the arms into place in the body and put the two middle hinge PTFE tubes in place |  |
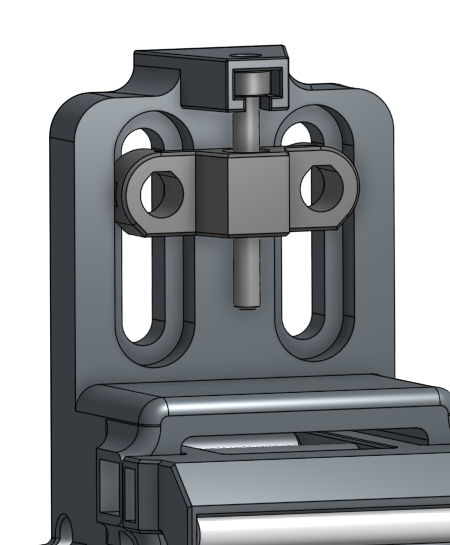
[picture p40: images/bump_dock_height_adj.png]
| Thread the height adjustment screw into the height adjuster and clip it into place |  |
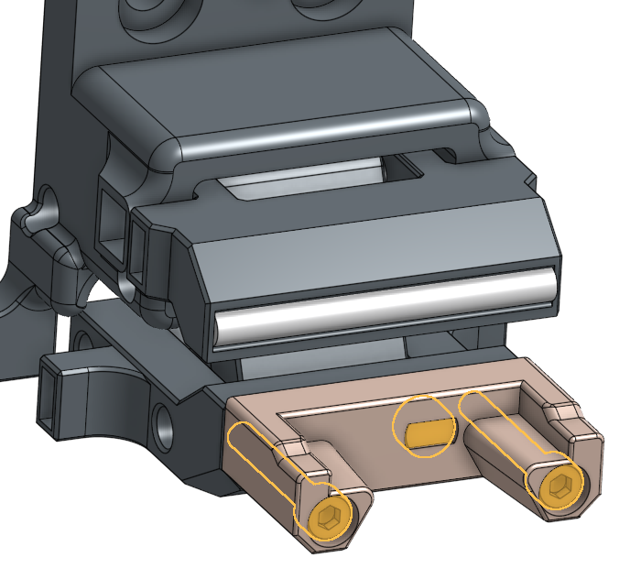
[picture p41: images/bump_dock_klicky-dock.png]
| Attach the Klicky dock to the bump dock. Don't forget the magnet and it's polarity if you have existing probes |  |
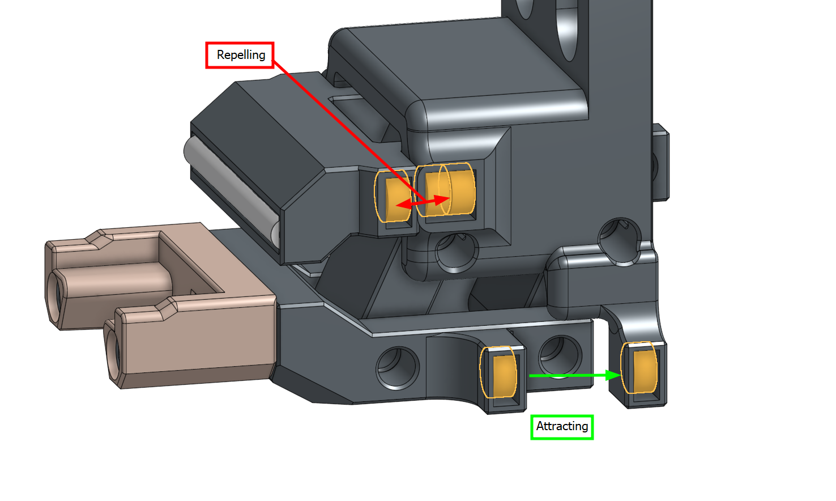
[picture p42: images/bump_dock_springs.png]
| Install Magnets to be the "springs" and "latch"<br/> Depending on how strong your magnets are, and how well everything moves, you may only need these magnets on one side. The top three magnets are setup to push the upper arm forward and the lower two magnets attract to pull the lower part backwards. |  |
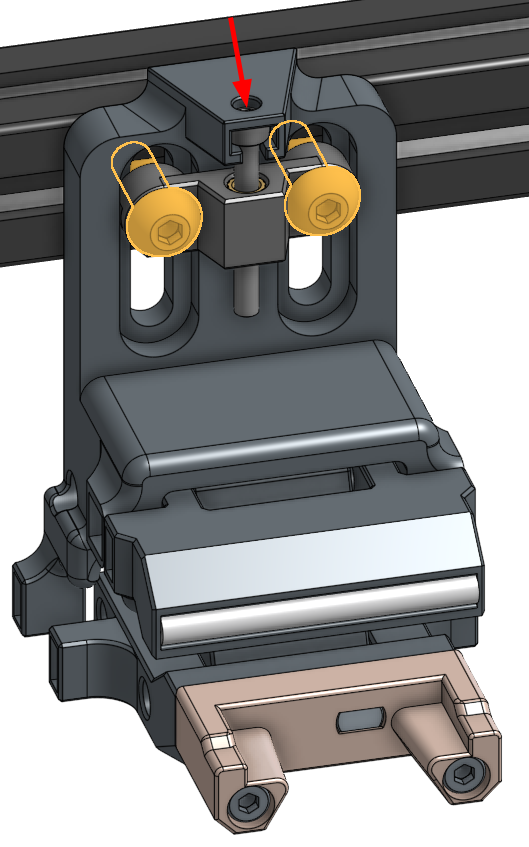
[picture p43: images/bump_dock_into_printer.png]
| Time to install it into the printer. |  |

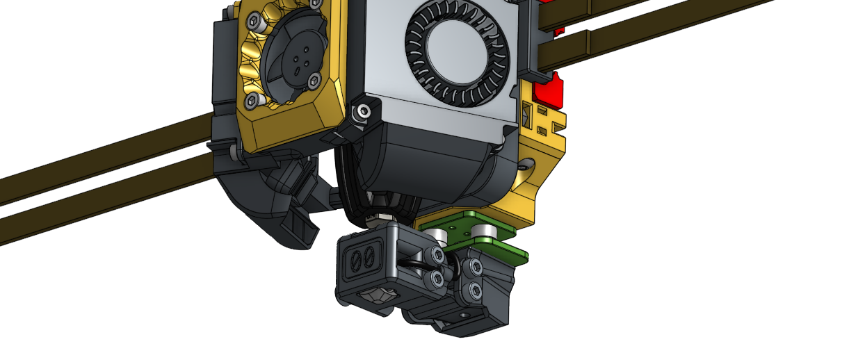
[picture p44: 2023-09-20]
images/PCB_Klicky-00_Xol-Toolhead_assembly.png

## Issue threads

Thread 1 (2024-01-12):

CAD files to adapt to cnc carriage

MaciejK98, 2024-01-12:
Hello, I've got a cnc carriage for 2.4 and it has different dimensions than the printed one. Would it be possible to share a cad files of the klicky00 body as I would like to see how I need to modify the pcb stealthburner klicky mount.
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

DW-Tas, 2024-01-15:
release candidate CAD has been uploaded.

Closed 2024-01-15.

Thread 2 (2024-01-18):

Stealth Burner edition with all M3 hardware?

PhilBaz, 2024-01-18:
Hello,

Just wanted to ask if it's possible to transition the stealthburner edition (at least the D2f)  to all M3 hardware? Then it really will only include stuff we all have lying around. Probably 95% of voron owners don't have any M2.5 hardware. If everything was m3 that would make it instantly available to every Voron user and help with wider adoption.

Just looking at the project from my perspective--a steallthburner + klicky + Auto-Z user, I'm most likely to choose the stealthburner D2f route as the path of least resistance. I imagine that will be the case with the majority of Voron owners. But maybe not. Just a thought.

Interesting project, looking forward to trying it out. Thank you!

DW-Tas, 2024-05-05:
RC2 has just been uploaded and is M3 instead of 2.5.

PhilBaz, 2024-05-05:
@DW-Tas Ahh, amazing! I had no idea that was in the works...klicky-00 here I come!

Thank you!

Closed 2024-05-05.

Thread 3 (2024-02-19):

BumpDock CAD

gvasvari, 2024-02-19:
Hi, could you upload the BumpDock CAD as well?
I'd like to make an adaptation for the VzCNC-HevORT toolhead with Goliath hotend (currently building a Monolith AWD v2.4)
So far I made a toolhead mount on the Goliath duct for the Klicky-00 probe which seems to be working mechanically.

The problem with the BumpDock is that the upper arm - which has the PTFE insert on the outer face, towards the toolhead - collides with the rear fan duct elbow joint. I think I can make it work by shifting the 45deg chamfer of the arm further back. It is currently above the PTFE tube, but I see some room for change.

DW-Tas, 2024-02-23:
Sure, here it is <https://github.com/DW-Tas/Klicky-00/blob/main/CAD/Klicky-00_Bump-Dock_assembly.step>

Closed 2024-02-23.

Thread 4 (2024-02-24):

Missing PCB SB mount

HaernCalistinson, 2024-02-24:
Without looking closely at what I was actually printing (I NEVER do that).. I didn't realize that the SB mount in the STL folder (STL/Klicky-00_AB-SB_mount_centered.stl) is for the non-pcb klicky. I could be completely blind, but I don't see the one for the PCB klicky mount. I can grab the one from the klicky pcb repo, but figured I'd drop a heads up.

DW-Tas, 2024-02-25:
Hi. That's intentional. I haven't included one here, because I haven't modified the PCB klicky mount for SB.

Closed 2024-02-25.

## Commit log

2023-04-24 Initial upload
    [KlickyNG-0O_SB.step, KlickyNG-0O_Xol2.step, KlickyNG_00_Cap.stl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]
2023-04-28 Added Klicky-00 XOL
    [Klicky-00_Xol2 - Mantis Xol Sherpa - Carriage - Klicky-00.stl, Klicky-00_Xol2.step, KlickyNG-00_Cap.stl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]
2023-04-28 Rename some files
    [Klicky-00_Probe.stl, KlickyNG-00_Probe.stl, KlickyNG-00_Stealthburner - Probe_Body.stl]
2023-04-28 Klick-00 SB version
    [Klicky-00_SB - Probe_Body.stl, Klicky-00_SB.step, KlickyNG-0O_SB.step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]
2023-04-28 Re-add SB NG version
    [Klicky-00_SB - Probe_Body.stl, KlickyNG-00_SB.step]
2023-04-28 Updated CAD
    [Klicky-00_SB.step, Klicky-00_Xol2 - Mantis Xol Sherpa - Carriage.stl, Klicky-00_Xol2.step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]
2023-04-28 Update CAD
    [Klicky-00_Xol2.step, KlickyNG-00_SB.step, KlickyNG-00_Xol2.step]
2023-04-28 fix Xol2 Klicky-00 STL orientation
    [Klicky-00_Xol2 - Mantis Xol Sherpa - Carriage.stl]
2023-07-17 Create Klicky-00_Xol-Carriage - Probe_Body.stl
2023-07-17 Update Klicky-00_Xol-Carriage - Probe_Body.stl
2023-07-17 Create KlickyNG-00_Xol-Carriage - Probe_Body.stl
2023-07-17 Update KlickyNG-00_Xol-Carriage - Probe_Body.stl
2023-08-01 updated NG style caps
    [KlickyNG-00_Cap.stl, KlickyNG-00_Cap_2.7mm.stl]
2023-08-01 update xol-carriage NG style
    [KlickyNG-00_Cap-extra-thick.stl, KlickyNG-00_Cap.stl, KlickyNG-00_Cap_2.7mm-extra-thick.stl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]
2023-09-20 PCB_Klicky-00 swing-arm Alpha release
    [Klicky-00_Probe.stl, Klicky-00_SB - Probe_Body.stl, Klicky-00_Xol2 - Mantis Xol Sherpa - Carriage.stl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]
2023-09-20 bom fix
2023-09-21 Archetype test version
    [PCB_Klicky-00_parts_Xol-Toolhead.stl, PCB_Klicky-00_parts_archetype.stl]
2023-09-23 updated bump dock stl
2023-09-24 Lower arm printability updated - bump dock
2023-09-26 make bump dock 2mm taller for archetype long
2023-09-26 fix bump dock stl
2023-09-27 bump-dock fix shallow magnet slot
2023-09-27 bump-dock with magnet removal slots
2023-09-28 updated BOM fix screw-length error
2023-10-05 tighten low swing-arm magnet xol-toolhead version
    [PCB_Klicky-00_parts_Xol-Toolhead.stl]
2023-10-05 tighter low arm magnet - archetype
    [PCB_Klicky-00_parts_archetype.stl]
2023-10-09 beta 1 update
    [Klicky-00-Probe_Body-Archetype-D2F.stl, Klicky-00-Probe_Body-Archetype-Unklicky.stl, Klicky-00-Probe_Body-D2F.stl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]
2023-10-10 Added StealthBurner parts
    [Klicky-00-Probe_Body-SB-D2F.stl, Klicky-00-Probe_Body-SB-Unklicky.stl, Klicky-00-swingarms-SB-both.stl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]
2023-10-11 fix BOM qty 40mm PTFE
2023-11-21 upload test stealthburner arms for bump dock
    [Klicky-00_Bump-Dock_StealthBurner-Arms.stl]
2023-11-25 added styuls STL and exposed magnet standard Klicky rear
    [Klicky-00-Probe_Stylus-Unklicky.stl, Klicky-00-Rear_Body-Klicky.stl, Klicky-00-Rear_Body-Klicky[exposed magnets].stl]
2024-01-14 upload RC1 CAD
2024-02-23 bump dock step assembly
    [Klicky-00_Bump-Dock_assembly.step]
2024-05-04 RC2 release
    [Klicky-00-Probe_Body-Archetype-D2F.stl, Klicky-00-Probe_Body-Archetype-Unklicky.stl, Klicky-00-Probe_Body-D2F.stl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]
2024-05-05 RC2 CAD
2024-05-05 upload missing bump-dock STLs
    [Klicky-00_Bump-Dock_StealthBurner-Arms.stl]
2024-06-22 added swingarms for Xol one-piece carriage
    [Klicky-00_Xol_PCB_Swingarm_Lower.stl, Klicky-00_Xol_PCB_Swingarm_Lower[two-part_carriage].stl, Klicky-00_Xol_PCB_Swingarm_Lower_Buckshot.stl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]
2024-11-24 upload SLM nozzle plate STLs
    [Klicky-00_SLM_Nozzle_Plate.stl, Klicky-00_Xol_Countersunk_Buckshot_Front-Strike_SLM.stl]
2025-01-01 RC3 release
    [A4T-Xol - Buckshot - Klicky.3mf, A4T-Xol - Buckshot - PCB.3mf, A4T-Xol - D2F - Klicky.3mf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]
2025-01-01 replace 3mf with STLs for RC3
    [A4T-Xol - Buckshot - Klicky.3mf, A4T-Xol - Buckshot - PCB.3mf, A4T-Xol - Buckshot - PCB.stl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]
2025-01-02 re-upload bump dock files
    [Klicky-00_Bump-Dock_StealthBurner-Arms.stl]

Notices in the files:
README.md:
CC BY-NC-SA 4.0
